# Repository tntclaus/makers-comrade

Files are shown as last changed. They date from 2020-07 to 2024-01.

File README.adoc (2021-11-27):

= Komrade of Maker (universal CNC platform)

[.right]
.First prototype, build volume (mm) 580x580x580
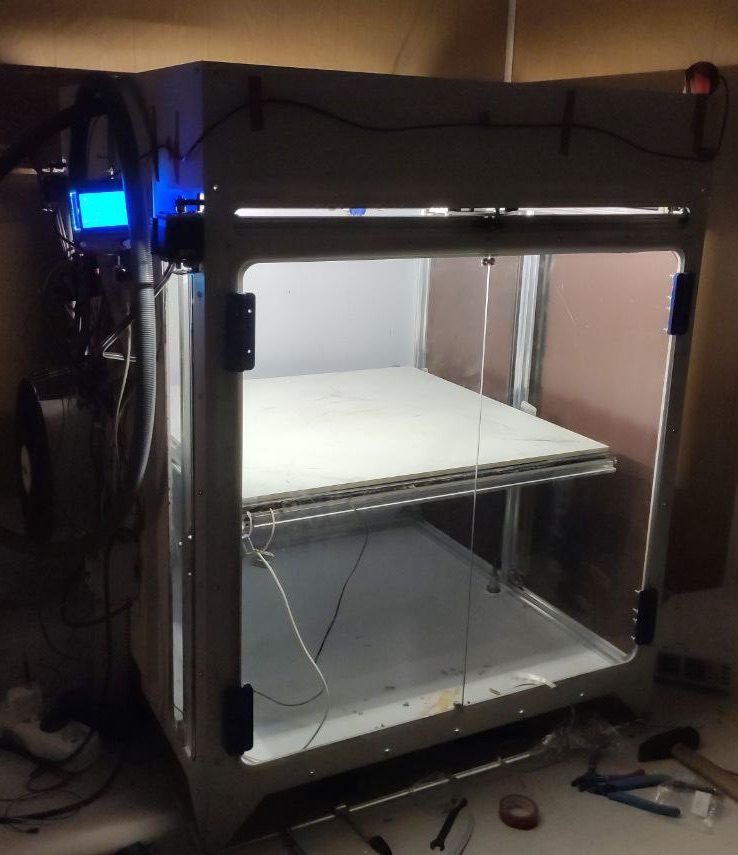
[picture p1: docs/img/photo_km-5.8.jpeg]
First prototype


This design is universal platform, that uses where available affordable parts, primarily from Reprap project, 8 bit realtime controllers, RPi 3/4 and Klipper.

Primary characteristics by application:

* 3D printing:
** Enclosed chamber passively heated up to 80ºC;
** Filament motion control;
** Auto bed levelling with Piezo Sensor and triple z axis;
** X/Y Linear speeds up to 200 mm/s (or greater with proper voltage/servos);
** Ceramic build surface.
* Milling with 585 series motors:
** Soft materials, e.g.: sheet plastics, plywood, aluminium (not tested);
** PCB prototyping.
* Laser cutting/engraving.
* Electrochemical machining.

== BOM
=== Base vitamins

.Base components common for all models
[cols="5,1,1,1",options="header",]
|===
|Part |Amount |Aliexpress |Amazon
|RAMPS 1.6+ |1 | - |-
|Arduino Mega |1 | - | -
|HDMI LCD 7" |1 | - | -
|RPi 3/4 |1 | - | -
|RPi Camera |1 | - | -
|RPi Motor Shield |1 | - | -
|Nema 17 steppers |5 | - | -
|X/Y axis MKS-Servo 42C |2 | - | -
|TMC 2209 |4 | - | -
|D16T parts set for universal X caret |1 | - | -
|V Slot Wheels|23 | - | -
|Steel parts for Z axis mount |1 | - | -
|Z axis axial bearing | 3 | - | -
|Z axis flexible coupler 5*8 |3 | - | -
|steel ball ø8mm |3 | - | -
|===

.Orbiter Extruder 3D Printer Toolhead
[cols="5,1,1,1",options="header",]
|===
|Part |Amount |Aliexpress |Amazon
|Extruder Orbiter with LDO stepper |1 | - | -
|Filament motion sensor |1 | - | -
|Crazy NF hotend | 1 | - | -
|===

=== Model KМ—3

Build Volume (mm): 300x300x300

[cols=",,,",options="header",]
|===
|Part |Amount |Aliexpress |Amazon
|  leadscrew  350 mm|  3  |  - | -
|  2020 VSlot extrusion 450 mm | 12 | - | -
|  2020 VSlot extrusion 850 mm | 4 | - | -
|  2040 VSlot extrusion 450 mm | 2 | - | -
|  GT6 Gates Belt (m) |  3  |  - | -
|===

=== Model KМ—6

Build Volume (mm): 600x600x600

== Dependencies

https://github.com/nophead/NopSCADlib
https://github.com/openscad/scad-utils
https://github.com/oysteinkrog/thing_libutils
https://github.com/Obijuan/obiscad

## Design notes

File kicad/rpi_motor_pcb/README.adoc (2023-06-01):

= Makers' Comrade CNC HAT

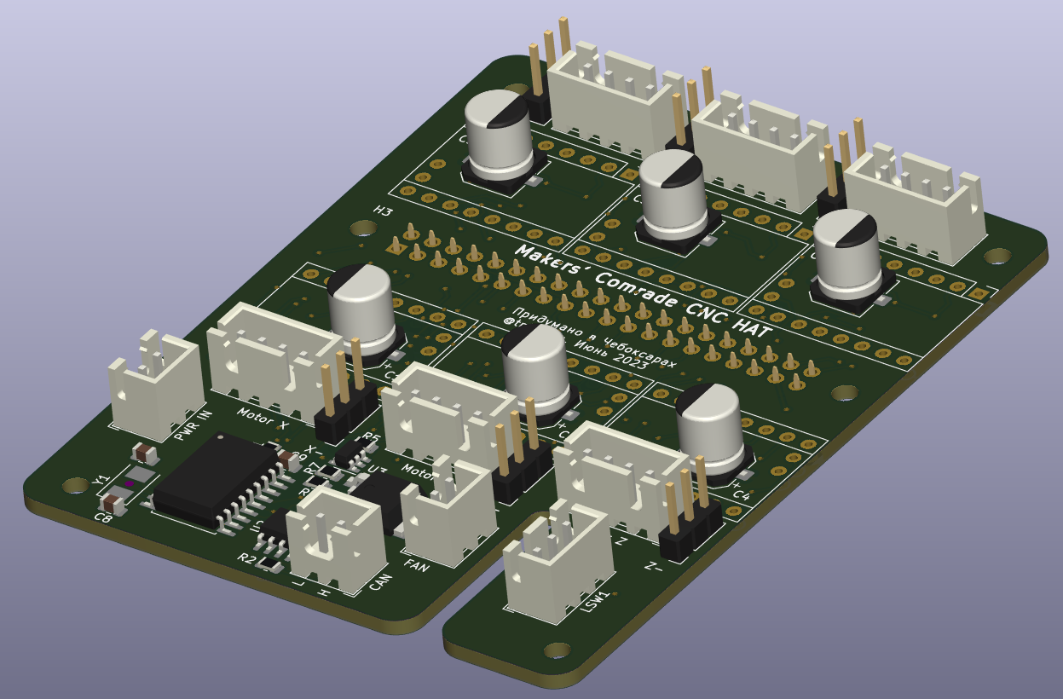
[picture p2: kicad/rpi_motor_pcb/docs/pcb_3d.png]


6-осевой ЧПУ шилд для Raspberry Pi 3B, 3B+, 4.

Возможности:

* Одновременное управление 6 драйверами шаговых двигателей:
** Поддерживаемые драйвера:
*** TMC2209, TMC2208 — режим UART с указанием адреса через перемычки MS1/MS2;
*** DRV8820, A4988 — обычный режим с конфигурацией через перемычки MS1,MS2,MS3;
* Любые другие драйвера, поддерживающие DIR/STEP.
* Суммарная пиковая производительность всех двигателей 1018 тыс. шагов/секунду (Klipper с патчем, Linux CNC не тестировался, но вероятно будет результат того же порядка).
* Поддержка концевиков для осей X, Y, Z, A, B, C как стандартного типа, так и DIAG выходов для без сенсорной парковки драйвера TMC2209.
* Поддержка дополнительного концевика (например, для датчика наличия/движения филамента 3д принтера).
* CANBUS host на базе MCP2515 и трансивера SN65HVD230:
** Даёт возможность гибкого дополнения станка периферией:
*** С контроллером экструдера https://github.com/makerbase-mks/MKS-THR36-THR42-UTC[MKS THR36] можно использовать как 3d принтер (не помешает canbus контроллер нагревательного стола/камеры).
*** С canbus контроллером шпинделя можно использовать как ЧПУ фрезер.
*** ...и т.д.
* Управление PWM нагрузкой с током до 1А (вентилятор обдува, маломощный двигатель).
* Поддерживаемые системы: Linux CNC, Klipper.

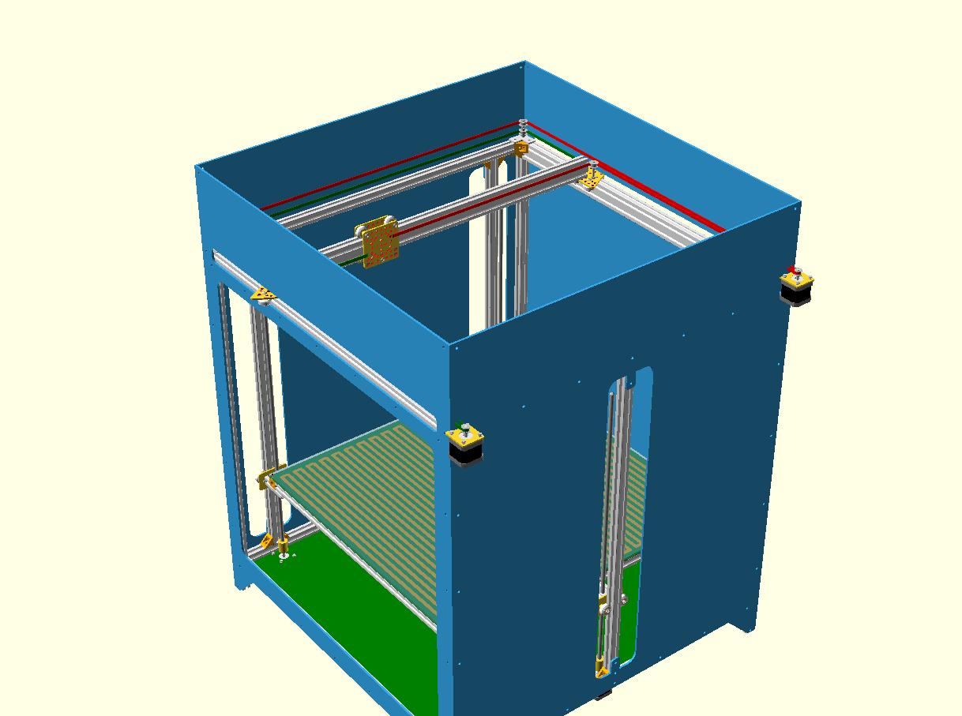
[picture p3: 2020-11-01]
scad/zap-3d-mk1.png

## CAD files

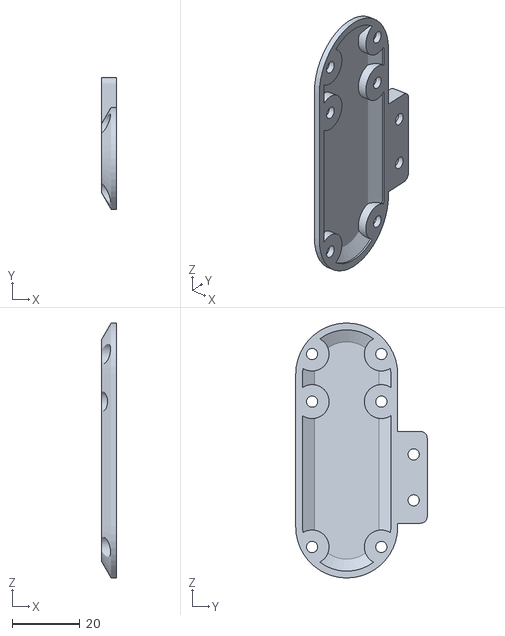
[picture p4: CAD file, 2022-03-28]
libstl/filament_sensor_cover_bmg.stl
4.55 x 38.7 x 75.0

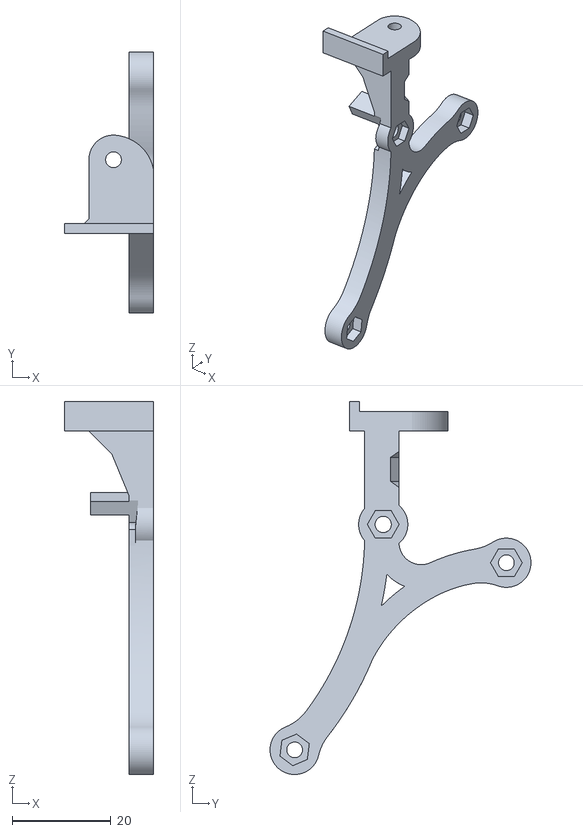
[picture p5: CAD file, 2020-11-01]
libstl/titan_vslot_bltouch_noctua_v2/Bras_fan.stl
18.2 x 53.0 x 75.7

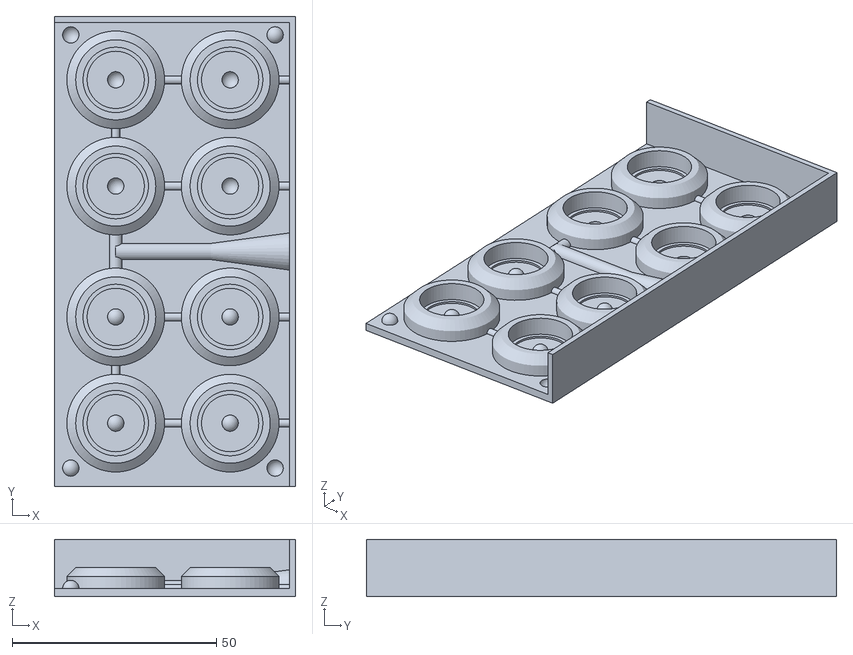
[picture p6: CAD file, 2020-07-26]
wheels_mold/v.4/wheels-mold.v4.stl
59.0 x 115.0 x 14.0

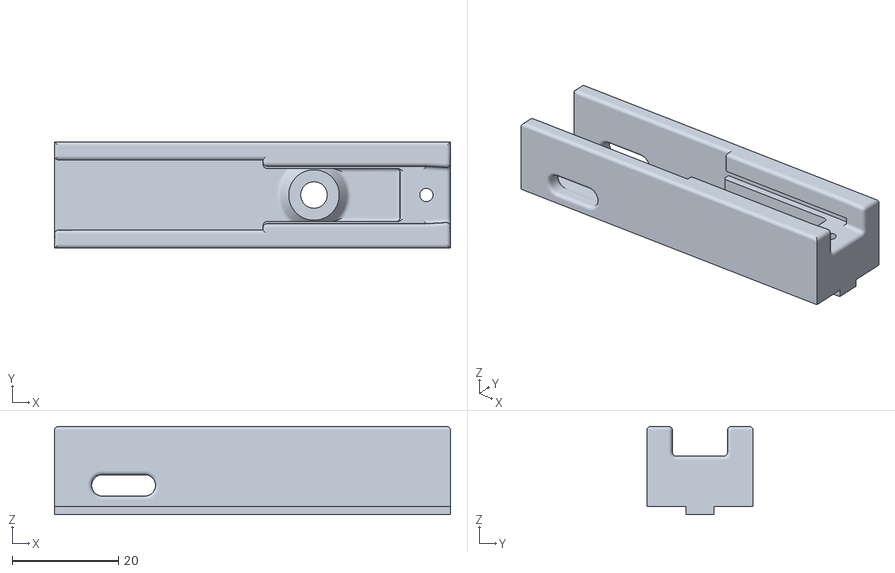
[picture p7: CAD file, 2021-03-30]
libstl/pp_uni_2.75_holder.stl
74.5 x 20.0 x 16.6

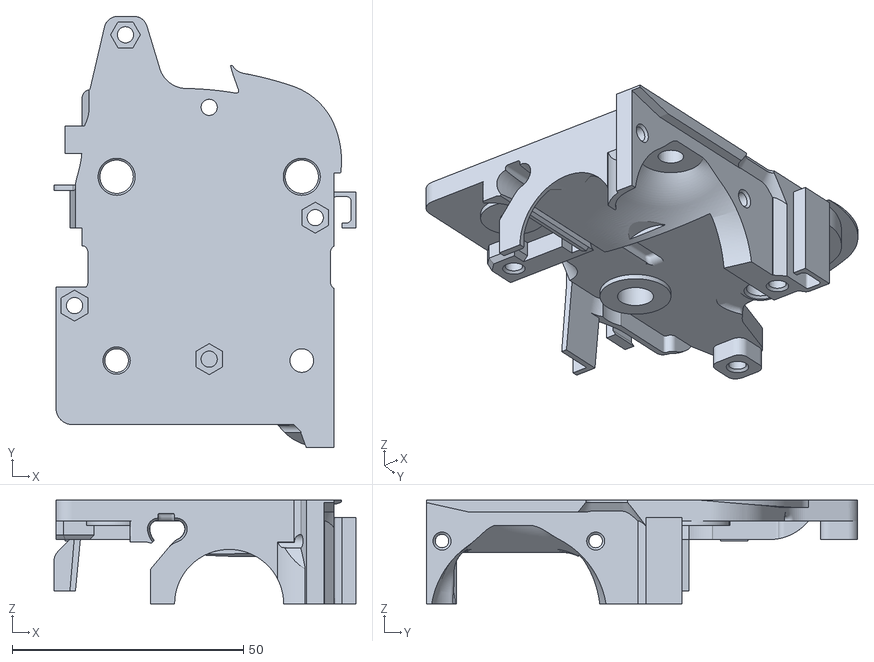
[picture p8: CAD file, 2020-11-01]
libstl/titan_vslot_bltouch_noctua_v2/Adapt_carriage.stl
65.2 x 93.2 x 22.4

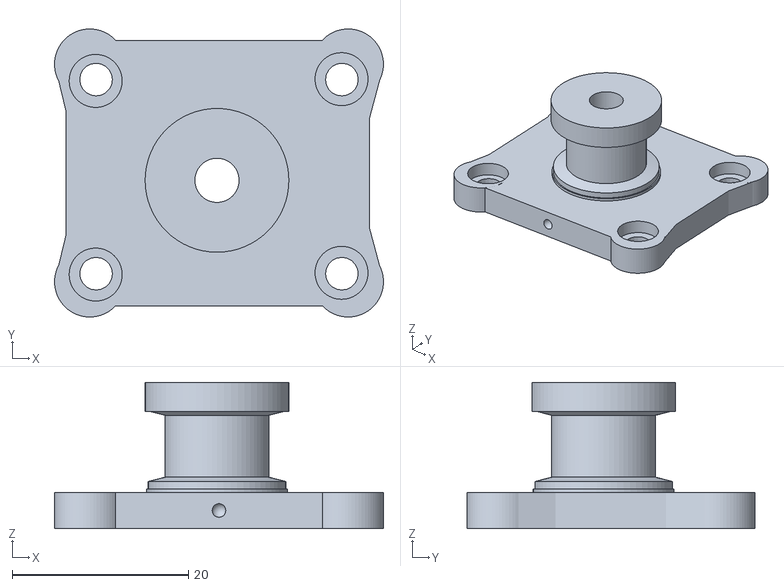
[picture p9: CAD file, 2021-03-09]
libstl/preicision_piezo_throat.stl
37.3 x 32.7 x 16.6

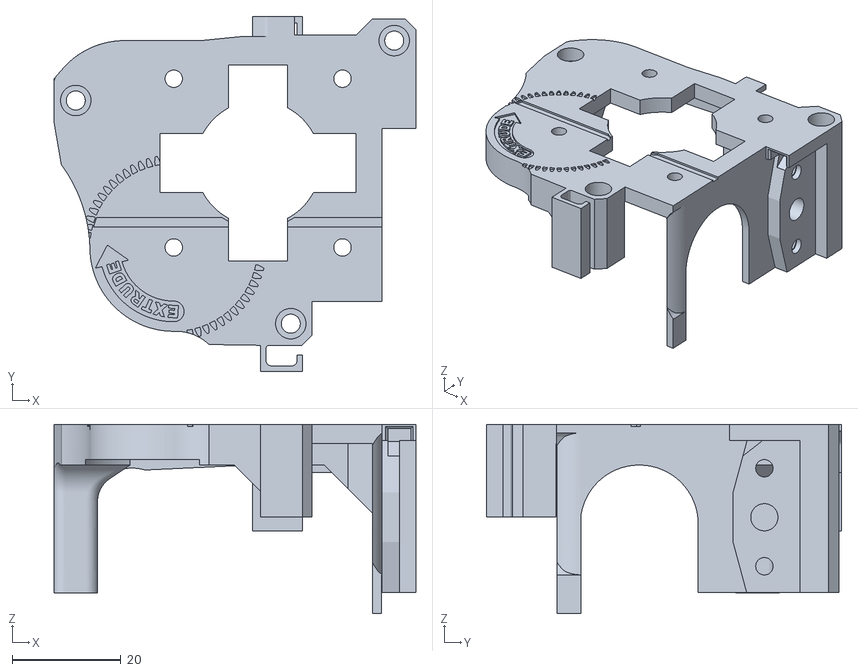
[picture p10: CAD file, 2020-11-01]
libstl/titan_vslot_bltouch_noctua_v2/Cover_titan.stl
66.5 x 65.2 x 34.8

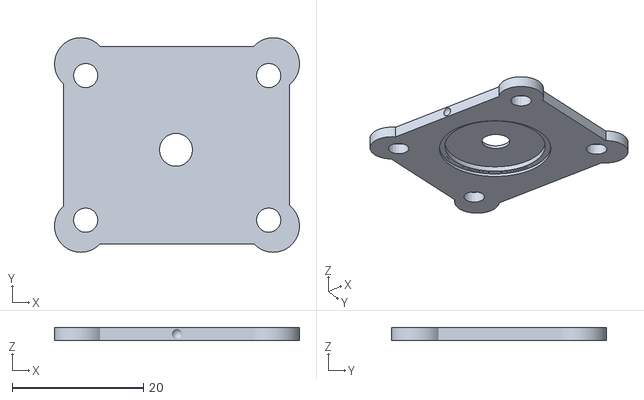
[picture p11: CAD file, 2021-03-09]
libstl/preicision_piezo_throat_bottom.stl
37.3 x 32.7 x 2.00

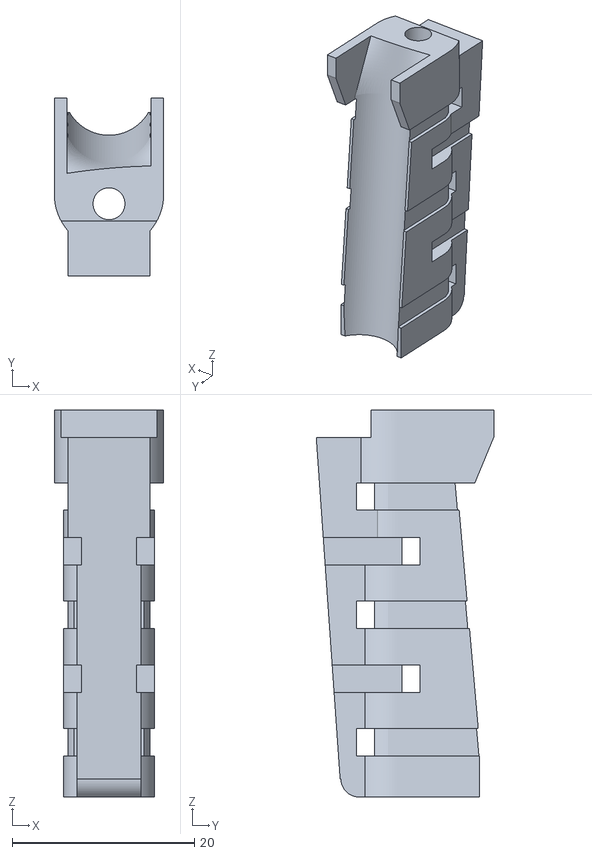
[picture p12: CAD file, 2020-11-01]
libstl/titan_vslot_bltouch_noctua_v2/Attache_cable.stl
12.0 x 19.5 x 42.5

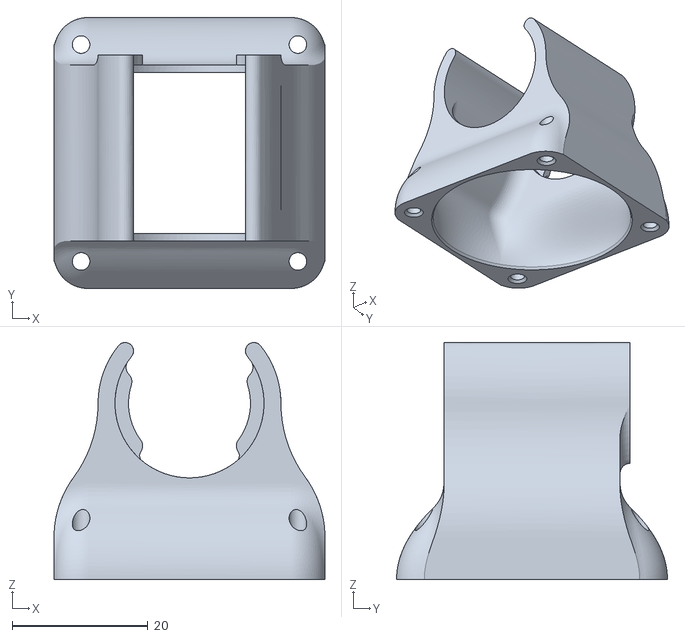
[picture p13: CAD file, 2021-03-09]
libstl/E3D_V6_40mm_Fan_v2.stl
40.0 x 40.0 x 35.0

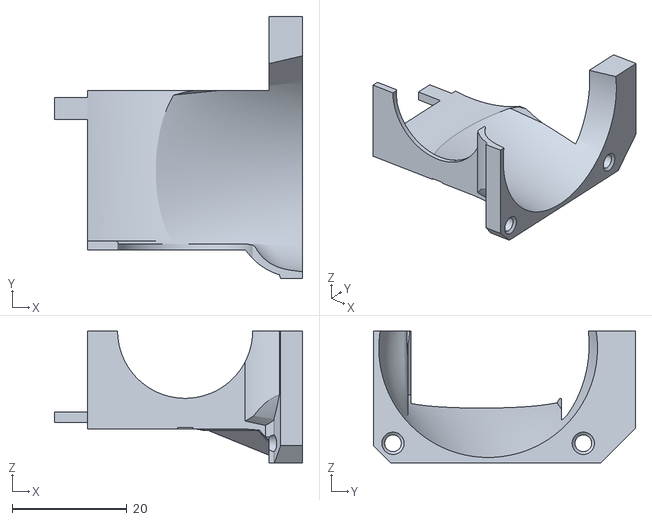
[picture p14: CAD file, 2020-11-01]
libstl/titan_vslot_bltouch_noctua_v2/Cover_e3d.stl
43.3 x 45.7 x 23.0

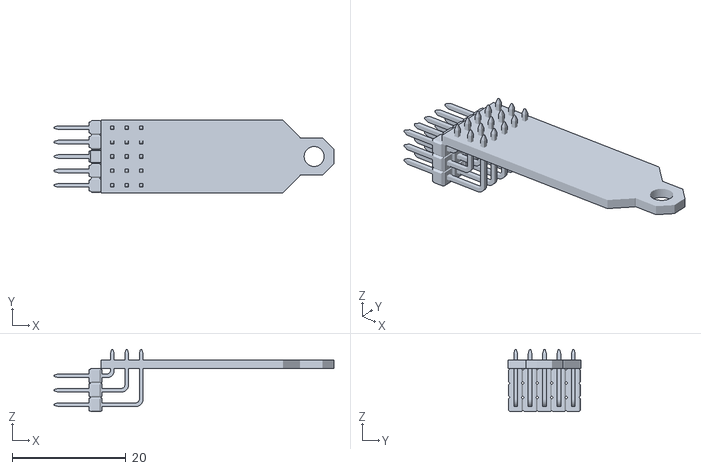
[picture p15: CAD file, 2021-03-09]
libstl/precision-piezo-uniboard2.75.stl
49.3 x 12.8 x 11.0

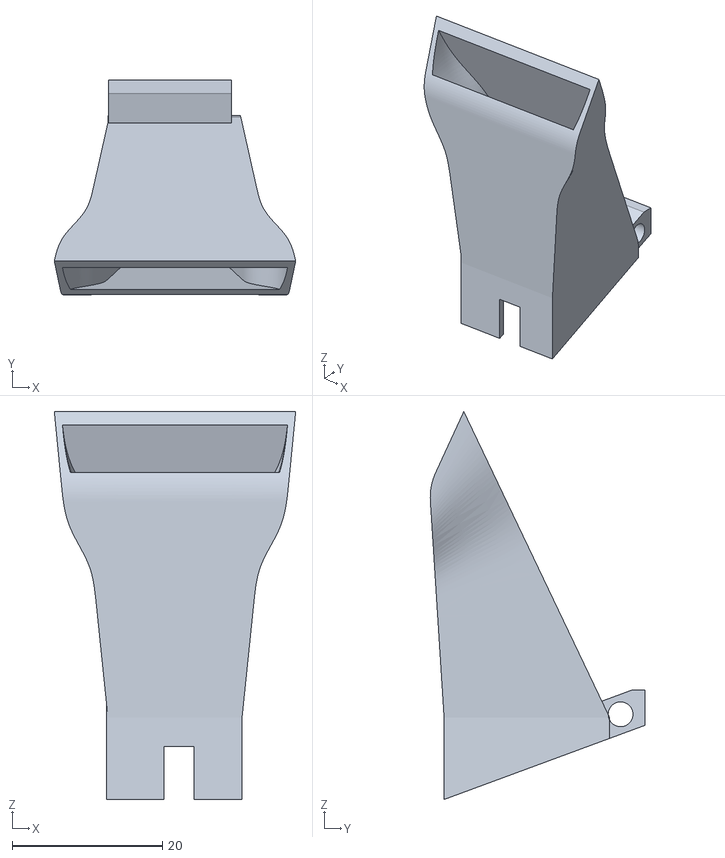
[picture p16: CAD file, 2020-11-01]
libstl/titan_vslot_bltouch_noctua_v2/Fan_duct.stl
32.1 x 28.5 x 51.6

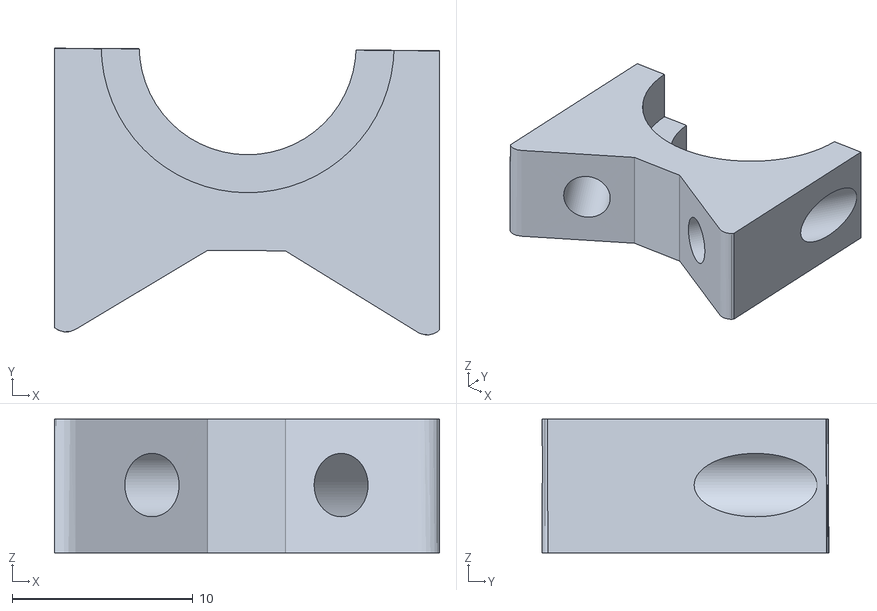
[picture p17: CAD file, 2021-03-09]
libstl/preicision_piezo_holder_inlet.stl
21.3 x 15.9 x 7.40

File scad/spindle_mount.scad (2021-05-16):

include <NopSCADlib/core.scad>
include <NopSCADlib/utils/rounded_polygon.scad>
include <NopSCADlib/vitamins/screws.scad>


include <../lib/utils.scad>
include <../lib/spindle/spindles.scad>

use <../lib/modularHoseLibrary.scad>
use <toolhead_utils.scad>

show_hose = false;


function TOOLHEAD_SPINDLE_RS895_VERTICAL_SCREW_MOUNTS(x = 30, y = 18) = [
    [ x,  y],
    [ x, -y],
    [-x,  y],
    [-x, -y],
];

coolant_hose_size = 20;
coolant_hose_size_out = coolant_hose_size+4;
coolant_hose_out_wall_dia = coolant_hose_size_out+2;

module motor_collet_44_100_30_RS895_stl() {
    $fn=180;
    
    motor_collet(
    width = 44, 
    length = 100, 
    heigth = 30, 
    type = RS895);
}

module motor_collet(width, length, heigth, wall_thickness = 30, type) {
    stl(
        str(
        "motor_collet","_",
        "W", width,"x",
        "L", length,"x",
        "H", heigth, "_",
        type[0])
    );
    
    
    collet_size = SPINDLE_motor_shield_diameter(type)+wall_thickness;
    
    color("#1111ff")
    render()
    difference() {
        cylinder(d = collet_size, h = heigth);
        translate_z(-1/2)
        cylinder(d = SPINDLE_motor_shield_diameter(type)+0.5, h = heigth+1);
        
        // половина
        translate([-collet_size/2+10, 0,collet_size])
        cube([collet_size, collet_size, collet_size*3], center = true);

        // срез сбоку
        translate([0, -collet_size/2-width/2,collet_size])
        cube([collet_size, collet_size, collet_size*3], center = true);

        // срез сбоку
        translate([0, collet_size/2+width/2,collet_size])
        cube([collet_size, collet_size, collet_size*3], center = true);

        // срез в центре
        translate([0, 0,collet_size])
        cube([collet_size, collet_size/3, collet_size*3], center = true);
        
        plate_corner_position(collet_size, width, 5);
        
        toolhead_screw_mount_locations(TOOLHEAD_SPINDLE_RS895_VERTICAL_SCREW_MOUNTS(),-heigth/2)
            cylinder(d = 4.01, h = heigth*2);

    }
}

module D16T_motor_mount_bottom_plate_W60xL100_IL80_ID8_CH8_VH11_RS895_dxf() {
    $fn = 180;
    motor_mount_bottom_plate_sketch(60, 100, 80, 8, 8, 11, RS895);
}

module D16T_motor_mount_top_plate_W60xL100_IL80_CH8_VH11_RS895_dxf() {
    $fn = 180;
    motor_mount_top_plate_sketch(60, 100, 80, 8, 11, RS895);
}

module motor_mount_bottom_plate_sketch(
    width, 
    length, 
    inset_length, 
    inset_depth, 
    coolant_hose_size,
    vacuum_hose_size,
    type) {
    coolant_hose_position = hose_position(length+1, coolant_hose_size, m=1);
    vacuum_hose_position = hose_position(length+5, vacuum_hose_size);


    difference() {
        toolhead_bottom_plate_sketch(width, length, inset_length, inset_depth);
        SPINDLE_cutouts(type);
        
        translate(coolant_hose_position)
        hose_base_plate_drill_holes(coolant_hose_size, 25, 3.05);
                    
        translate(vacuum_hose_position)    
        hose_base_plate_drill_holes(vacuum_hose_size, 25, 3.05); 
 
         toolhead_screw_mount_locations(TOOLHEAD_SPINDLE_RS895_VERTICAL_SCREW_MOUNTS())
            circle(d = 3.01);       
    }
}



module motor_mount_bottom_plate(
    width, 
    length, 
    inset_length, 
    inset_depth, 
    coolant_hose_size,
    vacuum_hose_size,
    type, 
    thickness = 3) {
    dxf(
        str(
        "D16T_motor_mount_bottom_plate","_",
        "W", width,"x",
        "L", length,"_",
        "IL", inset_length,"_",
        "ID", inset_depth,"_",
        "CH", coolant_hose_size, "_",
        "VH", vacuum_hose_size, "_",        
        type[0])
    );

    color("silver")
    translate_z(-3)
    linear_extrude(thickness)
    motor_mount_bottom_plate_sketch(
        width, 
        length, 
        inset_length, 
        inset_depth, 
        coolant_hose_size,
        vacuum_hose_size,
        type);
    coolant_hose_position = hose_position(length+1, coolant_hose_size, m=1);
    vacuum_hose_position = hose_position(length+5, vacuum_hose_size);


    
    plate_corner_position(width, length, 10)
    mount_magnet();
    
    
    if(show_hose) {
        translate_z(-thickness) {
            rotate([180,0,0]) translate(coolant_hose_position)
            coolant_hose_chain(coolant_hose_size);

            rotate([180,0,0]) translate(vacuum_hose_position)    
            rotate([0,0,180])
            vacuum_cleaner_hose_chain(vacuum_hose_size);
        }
    }
}

module motor_mount_top_plate_sketch(
        width, length, inset_length,
        coolant_hose_size,
        vacuum_hose_size, 
        type,
        thickness = 3
    ) {
    coolant_hose_position = hose_position(length+3, coolant_hose_size, m=1);
    vacuum_hose_position = hose_position(length+10, vacuum_hose_size);


    difference() {
        toolhead_top_plate_sketch(width, inset_length);
        circle(d = SPINDLE_motor_shield_diameter(type));
        

        translate(coolant_hose_position) hull() {
            circle(d = coolant_hose_size+4);
            translate([coolant_hose_size, 0, 0])
            circle(d = coolant_hose_size+4);
        }
                
        translate(vacuum_hose_position) hull() {   
            circle(d = vacuum_hose_size+4);
            translate([-vacuum_hose_size, 0, 0])
            circle(d = vacuum_hose_size+4);
        }
        
        toolhead_screw_mount_locations(TOOLHEAD_SPINDLE_RS895_VERTICAL_SCREW_MOUNTS())
            circle(d = 4.01);
    }    
}

module motor_mount_top_plate(
        width, length, inset_length,
        coolant_hose_size,
        vacuum_hose_size, 
        type,
        thickness = 3
    ) {
    dxf(
        str(
        "D16T_motor_mount_top_plate","_",
        "W", width,"x",
        "L", length,"_",
        "IL", inset_length,"_",
        "CH", coolant_hose_size, "_",
        "VH", vacuum_hose_size, "_",     
        type[0])
    );

    color("#aaaaaa")
    linear_extrude(thickness)
    motor_mount_top_plate_sketch(
        width, length, inset_length,
        coolant_hose_size,
        vacuum_hose_size, 
        type,
        thickness
    );
        
//    plate_corner_position(width, inset_length, 10)
//    translate_z(3)
//    mount_magnet();
//    translate([length/2-20, width/2-10, -2])
    toolhead_screw_mount_locations(TOOLHEAD_SPINDLE_RS895_VERTICAL_SCREW_MOUNTS())
    translate_z(-0.45)
    piezo_disc();
}

module coolant_hose_chain(size) {
    angle = 15;
    $fn = 20;
    color("blue") {
        translate_z(-3)
        rotate([180,0,0])
        hose_base_plate(size, 22, 3.05, 4.5);
        
        hose_base_plate(size, 22, 3.05, 4.5)
        rotate([0,angle,-angle])
        hose_segment(size)
        rotate([0,angle,-angle])
        hose_segment(size)
        rotate([0,-2*angle,-angle])
        hose_segment(size)
        rotate([0,-2*angle,angle])
        hose_segment(size)
        rotate([0,-2*angle,angle])
        hose_segment(size)
        rotate([0,-2*angle,2*angle])
        hose_round_nozzle(size, 3);
    }
}

module vacuum_cleaner_hose_chain(size) {
    angle = 15;
    $fn = 20;
    color("green") {
        translate_z(-3)
        rotate([180,0,0])
        hose_base_plate(size, 24, 3.05, 5.5);
        
        hose_base_plate(size, 24, 3.05, 5.5)
        rotate([0,angle,-angle])
        hose_segment(size)
        rotate([0,angle,-angle])
        hose_segment(size)
        rotate([0,-2*angle,-angle])
        hose_segment(size)
        rotate([0,-2*angle,angle])
        hose_segment(size)
        rotate([0,-2*angle,angle])
        hose_segment(size)
        rotate([0,-2*angle,2*angle])
        hose_flat_nozzle(size, size*2, size/2);
    }
}

module spindle_assembly(
        width, 
        length, 
        inset_length, 
        inset_depth, 
        heigth, 
        type = RS895
    ) {
    
    coolant_hose_size = 8;
    vacuum_hose_size = 12;

    toolhead_screw_mount_locations(TOOLHEAD_SPINDLE_RS895_VERTICAL_SCREW_MOUNTS(), 33)
        screw(M4_cap_screw, 35);

    
//    SPINDLE_ER11_assembly(type);
    motor_mount_bottom_plate(        
        width = width, length = length, inset_length = inset_length, type = type,
        coolant_hose_size = coolant_hose_size,
        vacuum_hose_size = vacuum_hose_size,
        inset_depth = inset_depth
    );    
    
    
    motor_collet(width-inset_depth*2, length, heigth, type = type);
    mirror([1,0,0])
    motor_collet(width-inset_depth*2, length, heigth, type = type);

    translate_z(heigth)
    motor_mount_top_plate(
        width = width, length = length, inset_length = inset_length, type = type,
        coolant_hose_size = coolant_hose_size,
        vacuum_hose_size = vacuum_hose_size
   );
}

//spindle_assembly(
//    width = 60, 
//    length = 100, 
//    inset_length = 80, 
//    inset_depth = 8, 
//    heigth = 30);

//D16T_motor_mount_bottom_plate_W60xL100_IL80_ID8_CH8_VH11_RS895_dxf();
//D16T_motor_mount_top_plate_W60xL100_IL80_CH8_VH11_RS895_dxf();
motor_collet_44_100_30_RS895_stl();

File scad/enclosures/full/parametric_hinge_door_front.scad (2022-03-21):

// -------------------------------------+---------------------------------------+---------------------------------------+---------------------------------------
// Title:        Parametric Caged Bearing
// Version:      3.7
// Release Date: 2019-12-14 (ISO 8601)
// Author:       Rohin Gosling
// -------------------------------------+---------------------------------------+---------------------------------------+---------------------------------------
//
// Description:
//
// - Parametric butt hinge, designed to be printed in one step.
//
// - While the entire working hinge may be printed in one step, it is also possible to disabled the internal fused pin, and leave a shaft
//   which may be used in the case where an external pin is desired.
//
// Release Notes:
//
// - Version 3.7
//   * Added a comment for the "knuckle_count" parameter, to notify users to always set an odd knuckle count in order to ensure that the unified
//     pin is supported by male knuckles on both ends. An even number of knuckles will leave one end of the unified pin unsupported by a male knuckle.
//   * Added a constraint to the "knuckle_count" parameter, to force an odd knuckle count. Even knuckle counts are now incemented to next odd number.
//     Example:
//     - A knuckle count of 4, will be incremented to 5.
//     - A knuckle count of 10 will, with be incremented to 11
//
// - Version 3.6
//   * Removed extended ASCII characters to make the source code compatible with the UTF-8 encoding required by the Thingiverse Customizer.
//
// - Version 3.5
//   * For hexagonal counterbores, the hexagonal cut has been rotated 90 degrees, to reduce the need for support material.
//     The overhang angle for hexagonal counterbore is 60 degrees.
//
// - Version 3.4
//   * Added support for linear and parabolic gusset curves.
//   * Factored out all SCG (Solid Constructive Geometry) overlap constants, and consolidated them into one global constant, "SCG_OVERLAP".
//
// - Version 3.3
//   * Placed pin shaft parameters into their own parameter group in the Thingiverse Customizer.
//
// - Version 3.2
//   * Added support for independently configurable top and bottom pin shaft counterbores.
//   * Added an assembly option to flip the model about the z-axis.
//     Usefull for viewing the top and bottom pin shaft counterbores.
//   * Configured the hinge throw angle Thingiverse Customizer parameter step size, to 5 degrees.
//
// - Version 3.1
//   * Added a counterbore feature for the pin shaft.
//     - While this feature may be enabled for one piece hinges that have the fused pin enabled, it is primarily designed for use with two
//       piece configurations that have their pin disabled. For instance, when the hinge is to be assembled using an external pin.
//     - In the case where a hinge is to be assembled using an external pin, it may be desired to have a pin shaft counterbore, where the end
//       caps of the knuckle joint array are counterbored, in order to allow the pin or bolt heads of the pin shaft, to be set flush with the
//       top and bottom edges of the hinge leaves.
//     - To accommodate both hexagonal and square bolt heads and nuts, the counterbore may be set to any one of circular, square or hexagonal.
//   * Added private text feature.
//     - A public parameter for the Thingiverse Customizer has not been added yet, however, users may set the 'text_enabled' local variable
//       in the 'leaf' module to 'true', which will enable a single row of inscribed text on each leaf.
//     - By default this feature will only work when exactly 4 fastener holes have been selected via the 'fastener_count' parameter, simply
//       because there is a nice open space available between the fastener holes for placing text, when 4 fastener holes are chosen.
//     - Text for the male and female leaves may be specified independently.
//
// - Version 3.0
//   * Added a parameter to disable the hinge pin, for when users would like to assemble with an external pin.
//   * Changed the main Thingiverse Customizer parameter group name from "Hinge Options", to "Assembly Options".
//   * Added a parameter to set the hinge throw angle.
//     Users can now set the throw angle, either for analysis and visualisation purposes, or for when the hinge is to be printed vertically
//     standing up on edge, in which case a throw angle of 120 degrees may be used to help keep the hinge stable on the build plate.
//   * Corrected spelling errors in the comments.
//
// - Version 2.9
//   * Added support for parabolic knuckle gussets to strengthen the knuckle joints.
//     Knuckle gussets may now be toggled on and off with the 'enable_knuckle_gusset' parameter.
//
// - Version 2.8
//   * Added the parameter, 'fastener_column_count', to enable single column fastener arrangements, that can be used for
//     piano hinge style fastener arrangements.
//
// - Version 2.7
//   * Rewrote the knuckle cutter module using mode generic math, that enables more parametizable control over knuckle joint
//     dimensions and configuration.
//
// - Version 2.6
//   * Added support for countersunk fastener holes. Now users can select either counterbore or countersunk.
//     dimensions and configuration.
//   * Started tracking release updates.
//
// - Version 1.0 - 2.5
//   * N/A - Release updates not tracked.
//
// -------------------------------------+---------------------------------------+---------------------------------------+---------------------------------------

// -------------------------------------+---------------------------------------+---------------------------------------+---------------------------------------
// Constants:
// -------------------------------------+---------------------------------------+---------------------------------------+---------------------------------------

// System constants.

C_CONSTANT = 0 + 0;     // Used to hide constant values from Thingiverse. Add to other constants to hide them as well.
C_NONE     = C_CONSTANT + 0;

// Leaf gender.

C_FEMALE   = C_CONSTANT + 0;
C_MALE     = C_CONSTANT + 1;

// SCG constants.

SCG_OVERLAP = C_CONSTANT + 0.01;    // Used for overlapping Boolean operations in order to avoid Boolean edge artefacts.
C_NEGATIVE  = C_CONSTANT + 0;       // Used for subtractive Boolean tools.
C_POSITIVE  = C_CONSTANT + 1;       // Used for additive Boolean tools.

// Bolt head shapes.

C_CIRCULAR  = C_CONSTANT + 0;
C_SQUARE    = C_CONSTANT + 1;
C_HEXAGONAL = C_CONSTANT + 2;

// Curve Type

C_FUNCTION_LINEAR    = C_CONSTANT + 1;      //  y = ax + b
C_FUNCTION_CIRCULAR  = C_CONSTANT + 2;      // r2 = x2 + y2
C_FUNCTION_PARABOLIC = C_CONSTANT + 3;      //  y = a2(x - j)2 + k    ...Vertex form.

// Minimum and maximum constraints.

C_MIN_HINGE_WIDTH                          = C_CONSTANT + 1.0;
C_MIN_HINGE_HEIGHT                         = C_CONSTANT + 1.0;
C_MIN_LEAF_GAUGE                           = C_CONSTANT + 1.0;
C_MIN_COMPONENT_CLEARENCE                  = C_CONSTANT + 0.1;
C_MAX_COMPONENT_CLEARENCE                  = C_CONSTANT + 1.0;
C_MIN_KNUCKLE_COUNT                        = C_CONSTANT + 3;
C_MAX_KNUCKLE_COUNT                        = C_CONSTANT + 15;
C_MIN_KNUCKLE_GUSSET_WIDTH                 = C_CONSTANT + 1.0;
C_MIN_FASTENER_MARGIN                      = C_CONSTANT + 1.0;
C_MIN_PIN_DIAMETER                         = C_CONSTANT + 1.0;
C_MIN_COUNTER_SINK_DEPTH_STOP              = C_CONSTANT + 1.0;
C_MIN_FASTENER_THREAD_DIAMETER             = C_CONSTANT + 0.0;
C_MIN_FASTENER_COUNT                       = C_CONSTANT + 3;
C_MIN_FASTENER_COLUMN_COUNT                = C_CONSTANT + 1;
C_MAX_FASTENER_COLUMN_COUNT                = C_CONSTANT + 2;
C_MIN_TESSELLATION                         = C_CONSTANT + 32;
C_MAX_TESSELLATION                         = C_CONSTANT + 256;
C_MIN_THROW_ANGLE                          = C_CONSTANT + -90;
C_MAX_THROW_ANGLE                          = C_CONSTANT + 180;
C_DEFAULT_THROW_ANGLE                      = C_CONSTANT + 0;
C_MIN_PIN_SHAFT_COUNTERBORE_DIAMETER       = C_CONSTANT + 0.1;
C_MIN_PIN_SHAFT_COUNTERBORE_WALL_THICKNESS = C_CONSTANT + 0.3;
C_MIN_PIN_SHAFT_COUNTERBORE_DEPTH          = C_CONSTANT + 0.0;
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

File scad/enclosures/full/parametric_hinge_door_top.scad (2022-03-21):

// -------------------------------------+---------------------------------------+---------------------------------------+---------------------------------------
// Title:        Parametric Caged Bearing
// Version:      3.7
// Release Date: 2019-12-14 (ISO 8601)
// Author:       Rohin Gosling
// -------------------------------------+---------------------------------------+---------------------------------------+---------------------------------------
//
// Description:
//
// - Parametric butt hinge, designed to be printed in one step.
//
// - While the entire working hinge may be printed in one step, it is also possible to disabled the internal fused pin, and leave a shaft
//   which may be used in the case where an external pin is desired.
//
// Release Notes:
//
// - Version 3.7
//   * Added a comment for the "knuckle_count" parameter, to notify users to always set an odd knuckle count in order to ensure that the unified
//     pin is supported by male knuckles on both ends. An even number of knuckles will leave one end of the unified pin unsupported by a male knuckle.
//   * Added a constraint to the "knuckle_count" parameter, to force an odd knuckle count. Even knuckle counts are now incemented to next odd number.
//     Example:
//     - A knuckle count of 4, will be incremented to 5.
//     - A knuckle count of 10 will, with be incremented to 11
//
// - Version 3.6
//   * Removed extended ASCII characters to make the source code compatible with the UTF-8 encoding required by the Thingiverse Customizer.
//
// - Version 3.5
//   * For hexagonal counterbores, the hexagonal cut has been rotated 90 degrees, to reduce the need for support material.
//     The overhang angle for hexagonal counterbore is 60 degrees.
//
// - Version 3.4
//   * Added support for linear and parabolic gusset curves.
//   * Factored out all SCG (Solid Constructive Geometry) overlap constants, and consolidated them into one global constant, "SCG_OVERLAP".
//
// - Version 3.3
//   * Placed pin shaft parameters into their own parameter group in the Thingiverse Customizer.
//
// - Version 3.2
//   * Added support for independently configurable top and bottom pin shaft counterbores.
//   * Added an assembly option to flip the model about the z-axis.
//     Usefull for viewing the top and bottom pin shaft counterbores.
//   * Configured the hinge throw angle Thingiverse Customizer parameter step size, to 5 degrees.
//
// - Version 3.1
//   * Added a counterbore feature for the pin shaft.
//     - While this feature may be enabled for one piece hinges that have the fused pin enabled, it is primarily designed for use with two
//       piece configurations that have their pin disabled. For instance, when the hinge is to be assembled using an external pin.
//     - In the case where a hinge is to be assembled using an external pin, it may be desired to have a pin shaft counterbore, where the end
//       caps of the knuckle joint array are counterbored, in order to allow the pin or bolt heads of the pin shaft, to be set flush with the
//       top and bottom edges of the hinge leaves.
//     - To accommodate both hexagonal and square bolt heads and nuts, the counterbore may be set to any one of circular, square or hexagonal.
//   * Added private text feature.
//     - A public parameter for the Thingiverse Customizer has not been added yet, however, users may set the 'text_enabled' local variable
//       in the 'leaf' module to 'true', which will enable a single row of inscribed text on each leaf.
//     - By default this feature will only work when exactly 4 fastener holes have been selected via the 'fastener_count' parameter, simply
//       because there is a nice open space available between the fastener holes for placing text, when 4 fastener holes are chosen.
//     - Text for the male and female leaves may be specified independently.
//
// - Version 3.0
//   * Added a parameter to disable the hinge pin, for when users would like to assemble with an external pin.
//   * Changed the main Thingiverse Customizer parameter group name from "Hinge Options", to "Assembly Options".
//   * Added a parameter to set the hinge throw angle.
//     Users can now set the throw angle, either for analysis and visualisation purposes, or for when the hinge is to be printed vertically
//     standing up on edge, in which case a throw angle of 120 degrees may be used to help keep the hinge stable on the build plate.
//   * Corrected spelling errors in the comments.
//
// - Version 2.9
//   * Added support for parabolic knuckle gussets to strengthen the knuckle joints.
//     Knuckle gussets may now be toggled on and off with the 'enable_knuckle_gusset' parameter.
//
// - Version 2.8
//   * Added the parameter, 'fastener_column_count', to enable single column fastener arrangements, that can be used for
//     piano hinge style fastener arrangements.
//
// - Version 2.7
//   * Rewrote the knuckle cutter module using mode generic math, that enables more parametizable control over knuckle joint
//     dimensions and configuration.
//
// - Version 2.6
//   * Added support for countersunk fastener holes. Now users can select either counterbore or countersunk.
//     dimensions and configuration.
//   * Started tracking release updates.
//
// - Version 1.0 - 2.5
//   * N/A - Release updates not tracked.
//
// -------------------------------------+---------------------------------------+---------------------------------------+---------------------------------------

// -------------------------------------+---------------------------------------+---------------------------------------+---------------------------------------
// Constants:
// -------------------------------------+---------------------------------------+---------------------------------------+---------------------------------------

// System constants.
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

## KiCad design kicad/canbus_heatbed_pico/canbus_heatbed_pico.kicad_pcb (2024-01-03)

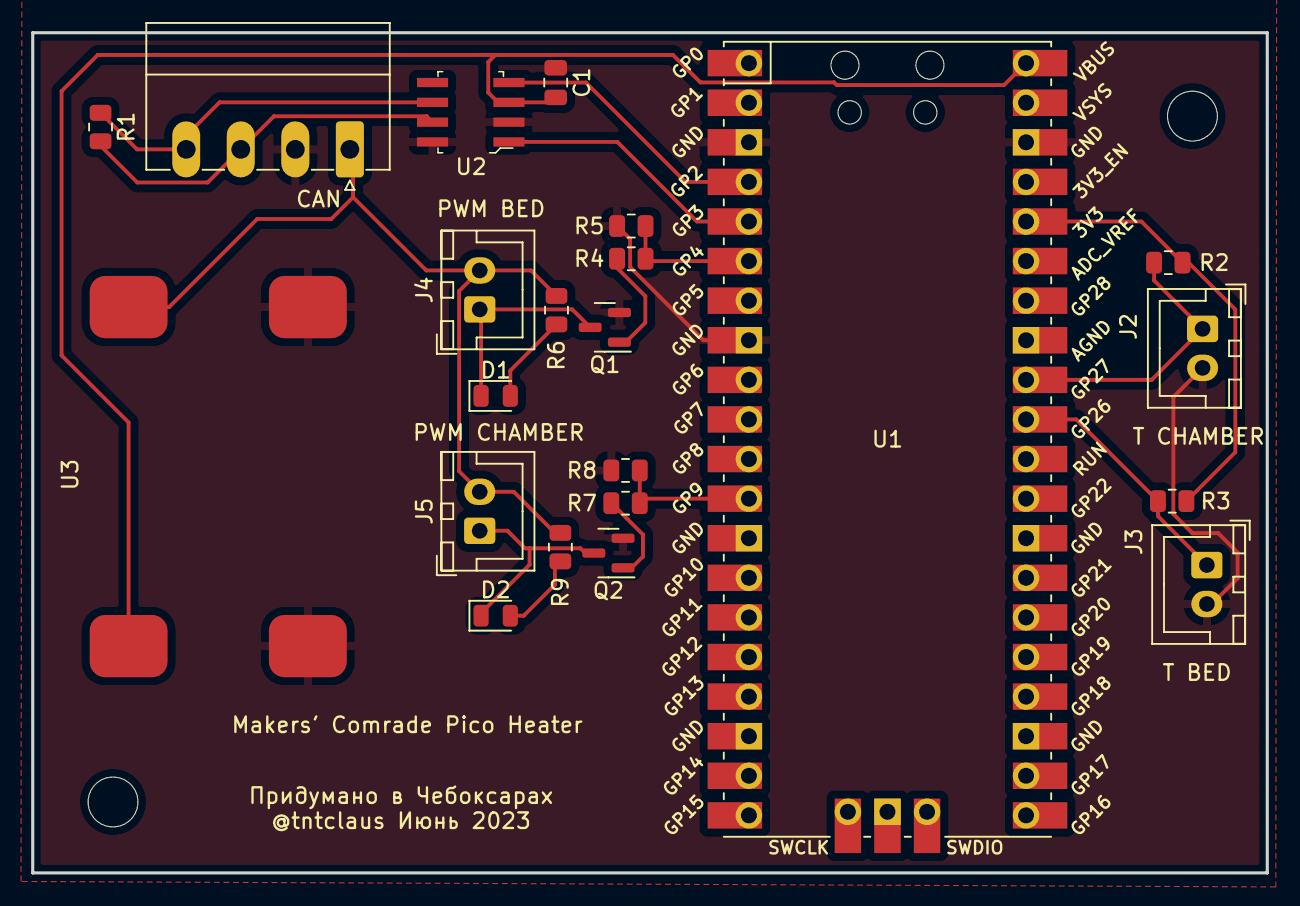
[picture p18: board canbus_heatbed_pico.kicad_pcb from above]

Board: 2 copper layers, 79.2 x 53.9 mm, 24 parts (0 on the bottom side), 18 nets.

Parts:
C1: 0.1µF; C_0805_2012Metric
D1, D2: XL-2012UGC; LED_0805_2012Metric
H1, H2: MountingHole; MountingHole_3.2mm_M3_DIN965
J1: CAN; PhoenixContact_MC_1,5_4-G-3.5_1x04_P3.50mm_Horizontal
J2: T CHAMBER; JST_XH_B2B-XH-A_1x02_P2.50mm_Vertical
J3: T BED; JST_XH_B2B-XH-A_1x02_P2.50mm_Vertical
J4: PWM BED; JST_XH_B2B-XH-A_1x02_P2.50mm_Vertical
J5: PWM CHAMBER; JST_XH_B2B-XH-A_1x02_P2.50mm_Vertical
Q1, Q2: 2N7002K; SOT-23
R1: 120; R_0805_2012Metric
R2, R3, R5, R6, R8, R9: 4.7k; R_0805_2012Metric
R4, R7: 200; R_0805_2012Metric
U1: Pico; RPi_Pico_SMD_TH
U2: SN65HVD230DR; SOIC-8_W3.9mm
U3: MP1584EN 5V; MP1584EN

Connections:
+3V3: R2.1, R3.1, U1.36 (3V3)
+5V: C1.2, U1.40 (VBUS), U2.3 (VCC), U3.1 (5V)
+24V: J1.1, J4.2, J5.2, R6.2, R9.2, U3.3 (Vin+)
/CAN_RX: U1.4 (GPIO2), U2.4 (R)
/CAN_TX: U1.5 (GPIO3), U2.1 (D)
/H: J1.4, R1.1, U2.6 (CANL)
/L: J1.3, R1.2, U2.7 (CANH)
/PWM BED: R4.1, R5.1, U1.6 (GPIO4)
/PWM CHAMBER: R7.1, R8.1, U1.12 (GPIO9)
/T BED: J3.1, R3.2, U1.31 (GPIO26_ADC0)
/T CHAMBER: J2.1, R2.2, U1.32 (GPIO27_ADC1)
GND: C1.1, J1.2, J2.2, J3.2, Q1.2 (S), Q2.2 (S), R5.2, R8.2, U1.3 (GND), U1.8 (GND), U1.38 (GND), U2.2 (GND), U2.8 (RS), U3.2 (GND), U3.4 (Vin-)
unnamed: D1.1 (K), J4.1, Q1.3 (D)
unnamed: D1.2 (A), R6.1
unnamed: D2.1 (K), J5.1, Q2.3 (D)
unnamed: D2.2 (A), R9.1
unnamed: Q1.1 (G), R4.2
unnamed: Q2.1 (G), R7.2

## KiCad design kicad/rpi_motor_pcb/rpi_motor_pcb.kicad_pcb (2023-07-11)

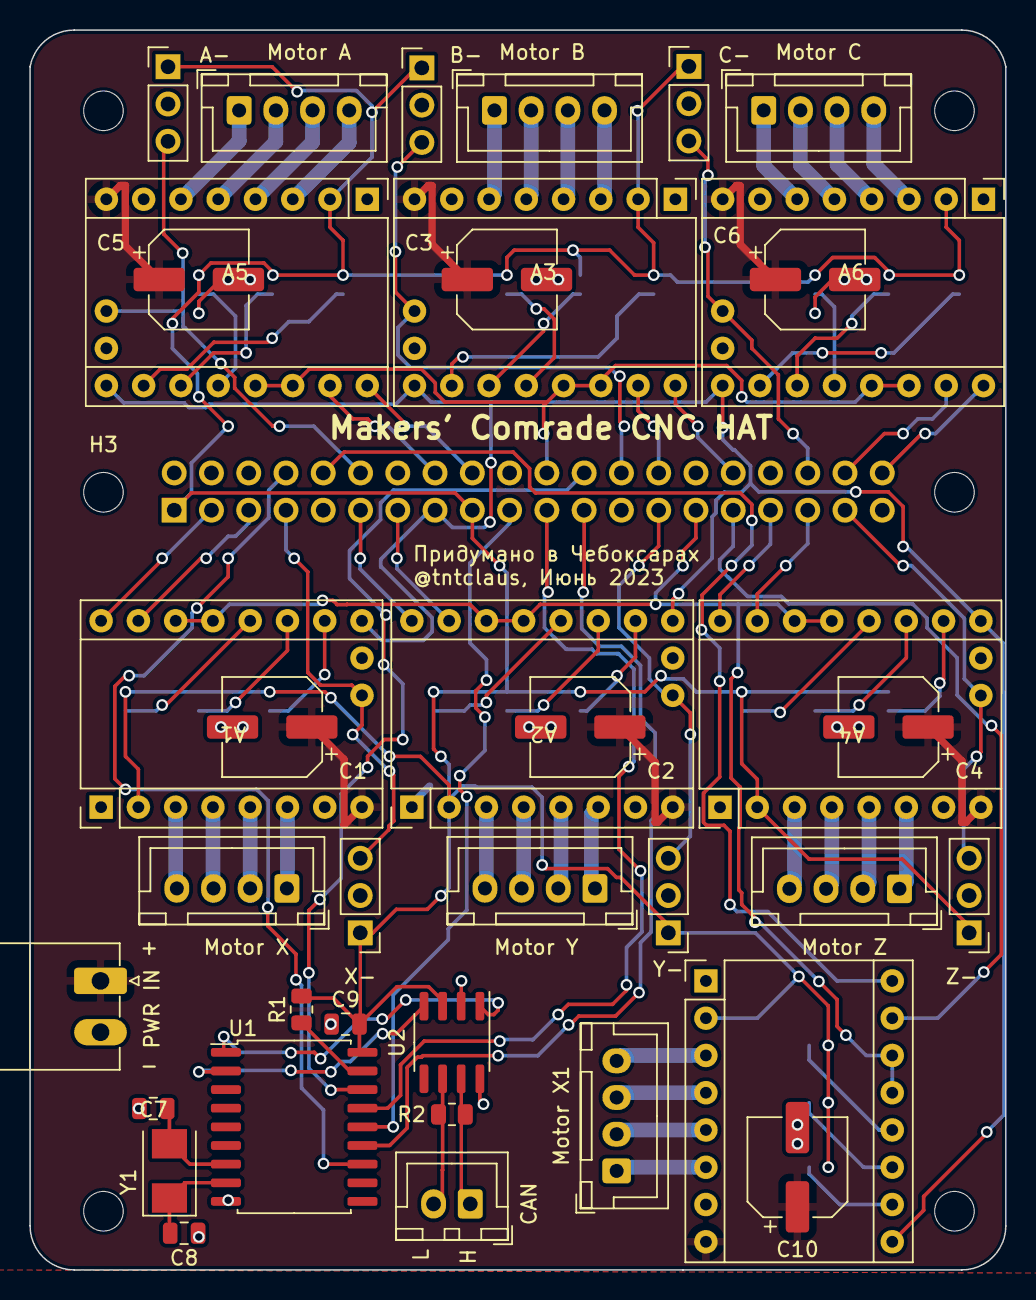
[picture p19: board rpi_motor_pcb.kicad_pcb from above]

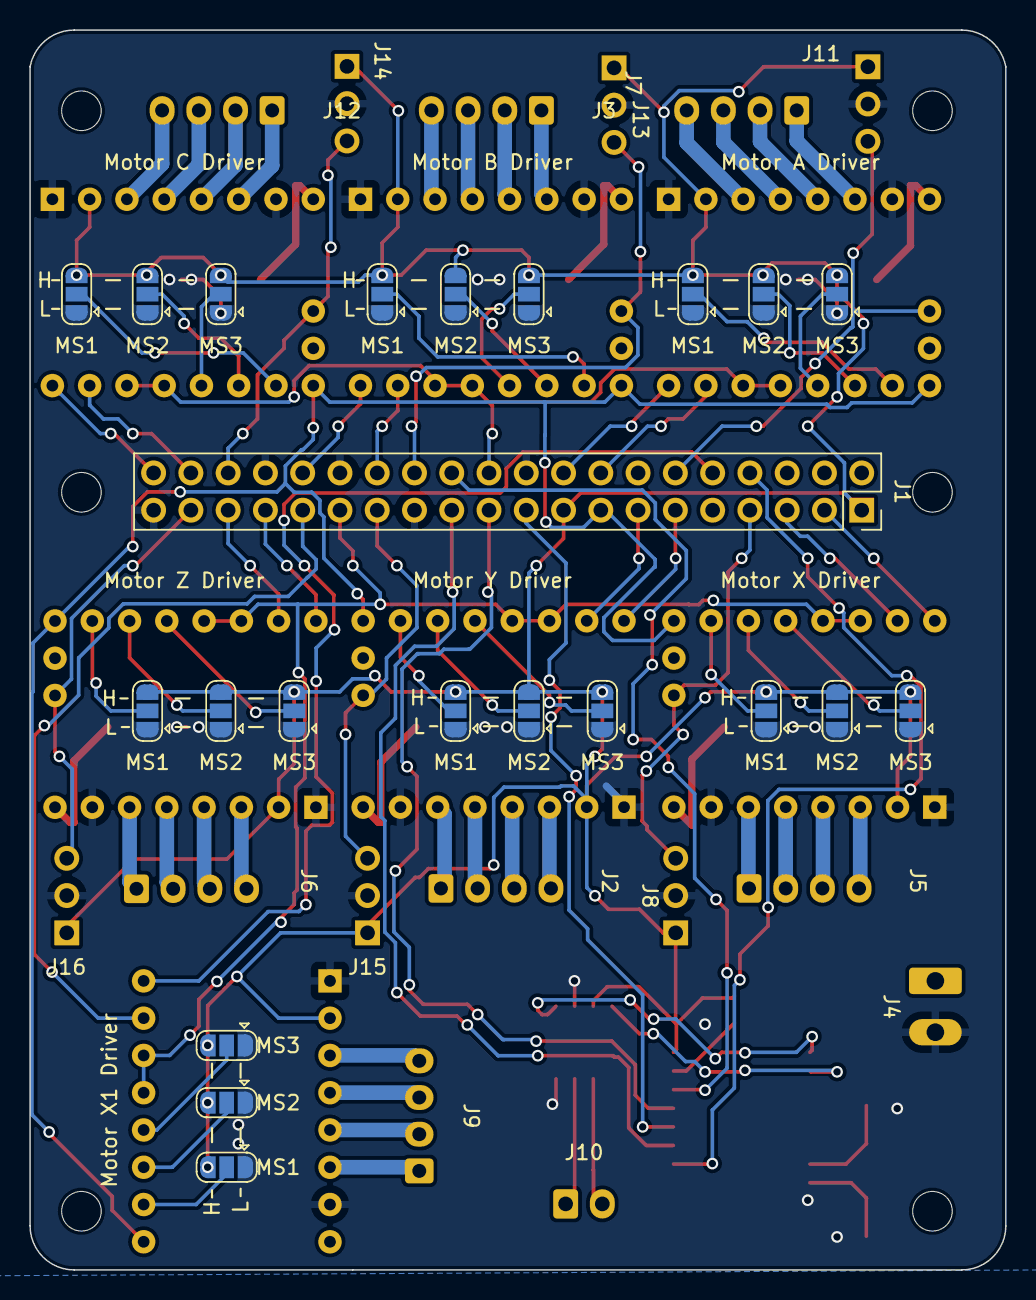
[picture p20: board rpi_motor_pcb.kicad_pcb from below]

Board: 2 copper layers, 66.5 x 84.5 mm, 65 parts (22 on the bottom side), 87 nets.

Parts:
A1: Motor X Driver; TMC220X
A2: Motor Y Driver; TMC220X
A3: Motor B Driver; TMC220X
A4: Motor Z Driver; TMC220X
A5: Motor A Driver; TMC220X
A6: Motor C Driver; TMC220X
A7: Motor X1 Driver; TMC2208
C1, C2, C3, C4, C5, C6, C10: 100µF 50V; CP_Elec_6.3x7.7
C7, C8: 22pF; C_0805_2012Metric
C9: 0.1µF; C_0805_2012Metric
H1, H2, H3, H4, H5, H6: MountingHole; MountingHole_2.7mm_M2.5_ISO14580
J1: Raspberry_Pi_2_3; PinSocket_2x20_P2.54mm_Vertical
J2: Motor Y; JST_XH_B4B-XH-A_1x04_P2.50mm_Vertical
J3: Motor B; JST_XH_B4B-XH-A_1x04_P2.50mm_Vertical
J4: PWR IN; PhoenixContact_MC_1,5_2-G-3.5_1x02_P3.50mm_Horizontal
J5: Motor X; JST_XH_B4B-XH-A_1x04_P2.50mm_Vertical
J6: Motor Z; JST_XH_B4B-XH-A_1x04_P2.50mm_Vertical
J7: Motor A; JST_XH_B4B-XH-A_1x04_P2.50mm_Vertical
J8: X-; PinHeader_1x03_P2.54mm_Vertical
J9: Motor X1; JST_XH_B4B-XH-A_1x04_P2.50mm_Vertical
J10: CAN; JST_XH_B2B-XH-A_1x02_P2.50mm_Vertical
J11: A-; PinHeader_1x03_P2.54mm_Vertical
J12: Motor C; JST_XH_B4B-XH-A_1x04_P2.50mm_Vertical
J13: B-; PinHeader_1x03_P2.54mm_Vertical
J14: C-; PinHeader_1x03_P2.54mm_Vertical
J15: Y-; PinHeader_1x03_P2.54mm_Vertical
J16: Z-; PinHeader_1x03_P2.54mm_Vertical
JP1, JP4, JP7, JP10, JP13, JP16, JP19: MS3; SolderJumper-3_P1.3mm_Open_RoundedPad1.0x1.5mm
JP2, JP5, JP8, JP11, JP14, JP17, JP20: MS2; SolderJumper-3_P1.3mm_Open_RoundedPad1.0x1.5mm
JP3, JP6, JP9, JP12, JP15, JP18, JP21: MS1; SolderJumper-3_P1.3mm_Open_RoundedPad1.0x1.5mm
R1: 10k; R_0805_2012Metric
R2: 120; R_0805_2012Metric
U1: MCP2515-xSO; SOIC-18W_7.5x11.6mm_P1.27mm
U2: SN65HVD230; SOIC-8_3.9x4.9mm_P1.27mm
Y1: Crystal; Crystal_SMD_5032-2Pin_5.0x3.2mm

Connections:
+3V3: A1.2 (VDD), A2.2 (VDD), A3.2 (VDD), A4.2 (VDD), A5.2 (VDD), A6.2 (VDD), A7.2 (VDD), C9.2, J1.1 (3V3), J1.17 (3V3), J8.1, J11.1, J13.1, J14.1, J15.1, J16.1, JP1.3 (B), JP2.3 (B), JP3.3 (B), JP4.3 (B), JP5.3 (B), JP6.3 (B), JP7.3 (B), JP8.3 (B), JP9.3 (B), JP10.3 (B), JP11.3 (B), JP12.3 (B), JP13.3 (B), JP14.3 (B), JP15.3 (B), JP16.3 (B), JP17.3 (B), JP18.3 (B), JP19.3 (B), JP20.3 (B), JP21.3 (B), R1.2, U1.18 (VDD), U2.3 (VCC)
/CAN/H: J10.1, R2.1, U2.7 (CANH)
/CAN/L: J10.2, R2.2, U2.6 (CANL)
/CAN/RX: U1.2 (RXCAN), U2.4 (R)
/CAN/TX: U1.1 (TXCAN), U2.1 (D)
/CAN_CS: J1.24 (~CE0/GPIO8), U1.16 (~CS)
/CAN_INT: J1.8 (GPIO14/TXD), U1.12 (~INT)
/CAN_MISO: J1.21 (MISO0/GPIO9), U1.15 (SO)
/CAN_MOSI: J1.19 (MOSI0/GPIO10), U1.14 (SI)
/CAN_SCK: J1.23 (SCLK0/GPIO11), U1.13 (SCK)
/MA DIAG: A5.18 (DIAG), J1.12 (GPIO18/PWM0), J11.3
/MA DIR: A5.16 (DIR), J1.18 (GPIO24)
/MA STEP: A5.15 (STEP), J1.16 (GPIO23)
/MB DIAG: A3.18 (DIAG), J1.26 (~CE1/GPIO7), J13.3
/MB DIR: A3.16 (DIR), J1.32 (PWM0/GPIO12)
/MB STEP: A3.15 (STEP), J1.28 (ID_SC/GPIO1)
/MC DIAG: A6.18 (DIAG), J1.36 (GPIO16), J14.3
/MC DIR: A6.16 (DIR), J1.40 (GPIO21/SCLK1)
/MC STEP: A6.15 (STEP), J1.38 (GPIO20/MOSI1)
/MX1 DIR: A7.16 (DIR), J1.10 (GPIO15/RXD)
/MX1 STEP: A7.15 (STEP), J1.31 (GCLK2/GPIO6)
/MX DIAG: A1.18 (DIAG), J1.7 (GCLK0/GPIO4), J8.3
/MX DIR: A1.16 (DIR), J1.3 (SDA/GPIO2)
/MX STEP: A1.15 (STEP), J1.5 (SCL/GPIO3)
/MY DIAG: A2.18 (DIAG), J1.27 (ID_SD/GPIO0), J15.3
/MY DIR: A2.16 (DIR), J1.11 (GPIO17)
/MY STEP: A2.15 (STEP), J1.13 (GPIO27)
/MZ DIAG: A4.18 (DIAG), J1.37 (GPIO26), J16.3
/MZ DIR: A4.16 (DIR), J1.33 (PWM1/GPIO13)
/MZ STEP: A4.15 (STEP), J1.35 (GPIO19/MISO1)
/Motor A/1A: A5.4 (1A), J7.3
/Motor A/1B: A5.3 (1B), J7.4
/Motor A/2A: A5.5 (2A), J7.2
/Motor A/2B: A5.6 (2B), J7.1
/Motor A/MS1: A5.10 (MS1), JP15.2 (C)
/Motor A/MS2: A5.11 (MS2), JP14.2 (C)
/Motor A/MS3: A5.12 (NC/TX), JP13.2 (C)
/Motor B/1A: A3.4 (1A), J3.3
/Motor B/1B: A3.3 (1B), J3.4
/Motor B/2A: A3.5 (2A), J3.2
/Motor B/2B: A3.6 (2B), J3.1
/Motor B/MS1: A3.10 (MS1), JP9.2 (C)
/Motor B/MS2: A3.11 (MS2), JP8.2 (C)
/Motor B/MS3: A3.12 (NC/TX), JP7.2 (C)
/Motor C/1A: A6.4 (1A), J12.3
/Motor C/1B: A6.3 (1B), J12.4
/Motor C/2A: A6.5 (2A), J12.2
/Motor C/2B: A6.6 (2B), J12.1
/Motor C/MS1: A6.10 (MS1), JP18.2 (C)
/Motor C/MS2: A6.11 (MS2), JP17.2 (C)
/Motor C/MS3: A6.12 (NC/TX), JP16.2 (C)
/Motor X1/1A: A7.4 (1A), J9.3
/Motor X1/1B: A7.3 (1B), J9.4
/Motor X1/2A: A7.5 (2A), J9.2
/Motor X1/2B: A7.6 (2B), J9.1
/Motor X1/MS1: A7.10 (MS1), JP21.2 (C)
/Motor X1/MS2: A7.11 (MS2), JP20.2 (C)
/Motor X1/MS3: A7.12 (NC/TX), JP19.2 (C)
/Motor X/1A: A1.4 (1A), J5.3
/Motor X/1B: A1.3 (1B), J5.4
/Motor X/2A: A1.5 (2A), J5.2
/Motor X/2B: A1.6 (2B), J5.1
/Motor X/MS1: A1.10 (MS1), JP3.2 (C)
/Motor X/MS2: A1.11 (MS2), JP2.2 (C)
/Motor X/MS3: A1.12 (NC/TX), JP1.2 (C)
/Motor Y/1A: A2.4 (1A), J2.3
/Motor Y/1B: A2.3 (1B), J2.4
/Motor Y/2A: A2.5 (2A), J2.2
/Motor Y/2B: A2.6 (2B), J2.1
/Motor Y/MS1: A2.10 (MS1), JP6.2 (C)
/Motor Y/MS2: A2.11 (MS2), JP5.2 (C)
/Motor Y/MS3: A2.12 (NC/TX), JP4.2 (C)
/Motor Z/1A: A4.4 (1A), J6.3
/Motor Z/1B: A4.3 (1B), J6.4
/Motor Z/2A: A4.5 (2A), J6.2
/Motor Z/2B: A4.6 (2B), J6.1
/Motor Z/MS1: A4.10 (MS1), JP12.2 (C)
/Motor Z/MS2: A4.11 (MS2), JP11.2 (C)
/Motor Z/MS3: A4.12 (NC/TX), JP10.2 (C)
/UART_A: A3.13 (PDN/RX), A3.14 (NC/CLK), A5.13 (PDN/RX), A5.14 (NC/CLK), A6.13 (PDN/RX), A6.14 (NC/CLK), J1.22 (GPIO25)
/UART_X: A1.13 (PDN/RX), A1.14 (NC/CLK), A2.13 (PDN/RX), A2.14 (NC/CLK), A4.13 (PDN/RX), A4.14 (NC/CLK), A7.13 (PDN/RX), A7.14 (NC/CLK), J1.29 (GCLK1/GPIO5)
GND: A1.1 (GND), A1.7 (GND), A2.1 (GND), A2.7 (GND), A3.1 (GND), A3.7 (GND), A4.1 (GND), A4.7 (GND), A5.1 (GND), A5.7 (GND), A6.1 (GND), A6.7 (GND), A7.1 (GND), A7.7 (GND), C1.2, C2.2, C3.2, C4.2, C5.2, C6.2, C7.1, C8.1, C9.1, C10.2, J1.20 (GND), J1.25 (GND), J1.30 (GND), J1.34 (GND), J1.39 (GND), J4.2, J8.2, J11.2, J13.2, J14.2, J15.2, J16.2, JP1.1 (A), JP2.1 (A), JP3.1 (A), JP4.1 (A), JP5.1 (A), JP6.1 (A), JP7.1 (A), JP8.1 (A), JP9.1 (A), JP10.1 (A), JP11.1 (A), JP12.1 (A), JP13.1 (A), JP14.1 (A), JP15.1 (A), JP16.1 (A), JP17.1 (A), JP18.1 (A), JP19.1 (A), JP20.1 (A), JP21.1 (A), U1.9 (VSS), U2.2 (GND), U2.8 (Rs)
MEN: A1.9 (~ENABLE), A2.9 (~ENABLE), A3.9 (~ENABLE), A4.9 (~ENABLE), A5.9 (~ENABLE), A6.9 (~ENABLE), A7.9 (~ENABLE), J1.15 (GPIO22)
unnamed: C7.2, U1.7 (OSC2), Y1.2
unnamed: C8.2, U1.8 (OSC1), Y1.1
unnamed: R1.1, U1.17 (~RESET)
Vin: A1.8 (VMOT), A2.8 (VMOT), A3.8 (VMOT), A4.8 (VMOT), A5.8 (VMOT), A6.8 (VMOT), A7.8 (VMOT), C1.1, C2.1, C3.1, C4.1, C5.1, C6.1, C10.1, J4.1

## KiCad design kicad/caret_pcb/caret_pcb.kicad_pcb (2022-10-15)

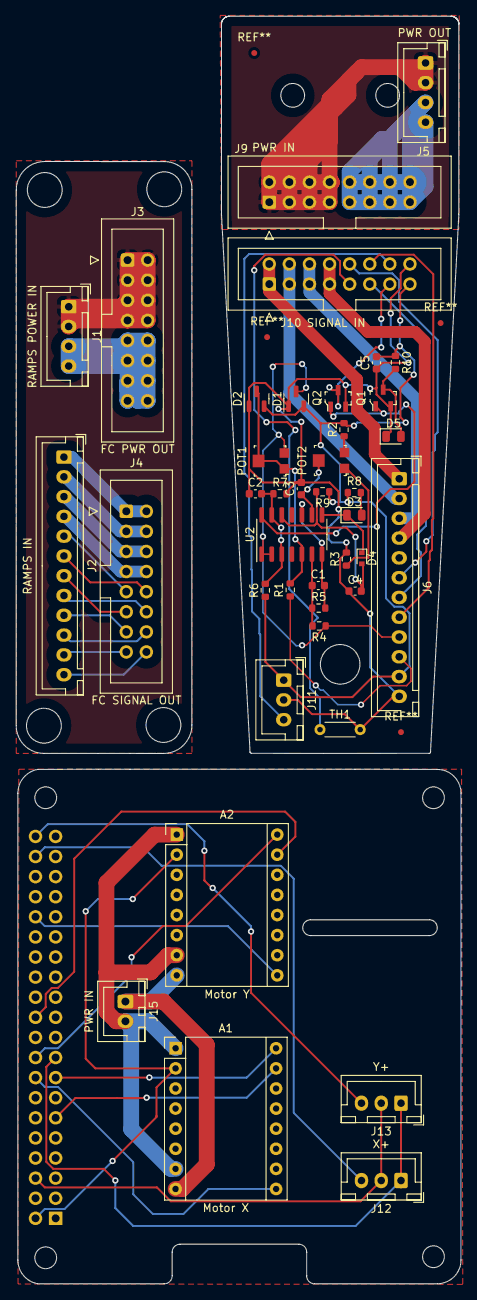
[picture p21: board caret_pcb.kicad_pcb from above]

Board: 2 copper layers, 56.2 x 160.2 mm, 41 parts (1 on the bottom side), 55 nets.

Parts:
A1: Motor X; Pololu_Breakout-16_15.2x20.3mm
A2: Motor Y; Pololu_Breakout-16_15.2x20.3mm
C1, C2, C3: 0.1uF; C_0603_1608Metric
C4, C5: 1 uF 10 V 10%; C_0603_1608Metric
D1, D2: BAV99; SOT-23
D3: RED; D_0805_2012Metric
D4: RB751S40T1G; D_SOD-523
D5: BLUE; D_0805_2012Metric
J1: RAMPS POWER IN; JST_XH_B4B-XH-A_1x04_P2.50mm_Vertical
J2: RAMPS IN; JST_XH_B12B-XH-A_1x12_P2.50mm_Vertical
J3: FC PWR OUT; IDC-Header_2x08_P2.54mm_Vertical
J4: FC SIGNAL OUT; IDC-Header_2x08_P2.54mm_Vertical
J5: PWR OUT; JST_XH_B4B-XH-A_1x04_P2.50mm_Vertical
J6: TOOLHEAD; JST_XH_B12B-XH-A_1x12_P2.50mm_Vertical
J9: PWR IN; IDC-Header_2x08_P2.54mm_Vertical
J10: SIGNAL IN; IDC-Header_2x08_P2.54mm_Vertical
J11: Endstop Y; JST_XH_B3B-XH-A_1x03_P2.50mm_Vertical
J12: X+; JST_XH_B3B-XH-A_1x03_P2.50mm_Vertical
J13: Y+; JST_XH_B3B-XH-A_1x03_P2.50mm_Vertical
J14: Raspberry_Pi_2_3; PinSocket_2x20_P2.54mm_Vertical
J15: PWR IN; JST_XH_B2B-XH-A_1x02_P2.50mm_Vertical
POT1: TC33X-2-105; Trimpot_3.8mmx3.6mm_TC33X-2-103E
POT2: TC33X-2-104; Trimpot_3.8mmx3.6mm_TC33X-2-103E
Q1, Q2: BSS138BK; SOT-23-3
R1, R6, R7: 10k; R_0603_1608Metric
R2: 330k; R_0603_1608Metric
R3: 390k; R_0603_1608Metric
R4: 20k; R_0603_1608Metric
R5: 82k; R_0603_1608Metric
R8: 510; R_0603_1608Metric
R9: 1M; R_0603_1608Metric
R10: 1k; R_0603_1608Metric
TH1: Thermistor_NTC; R_Axial_DIN0204_L3.6mm_D1.6mm_P5.08mm_Horizontal
U2: LM324; SOIC-14_3.9x8.7mm_P1.27mm

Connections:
/Caret Adapter/1A: J6.2, J10.3, J10.4
/Caret Adapter/1B: J6.1, J10.1, J10.2
/Caret Adapter/2A: J6.3, J10.5, J10.6
/Caret Adapter/2B: J6.4, J10.7, J10.8
/Caret Adapter/5V+: C5.2, D1.2 (A), D2.2 (A), J6.11, J10.15, J11.1, R2.2, R6.1, R8.1, R9.1, R10.1
/Caret Adapter/End.Y: J10.14, J11.3
/Caret Adapter/GND: C2.1, C3.2, C4.1, C5.1, D1.1 (K), D2.1 (K), D5.1 (K), J6.12, J10.16, J11.2, Q1.2 (S), Q2.2 (S), R3.2, R7.2, TH1.2
/Caret Adapter/HE0+: J5.1, J5.2, J9.1, J9.2, J9.3, J9.4, J9.5, J9.6, J9.7, J9.8
/Caret Adapter/PWM 5V: J6.8, J10.12
/Caret Adapter/PZ+: D1.3 (K), J6.9, POT1.3 (CW), R4.1, U2.1, U2.2 (-)
/Caret Adapter/PZ-: J6.10, R1.1
/Caret Adapter/T.enc: J10.9, TH1.1
/Caret Adapter/T.ext: J6.6, J10.10
/Caret Adapter/T.hbr: J6.7, J10.11
/Caret Adapter/Z+: J10.13, Q2.3 (D)
/RAMPS Adapter/+5V: J2.11, J4.15
/RAMPS Adapter/A3/T.hbr: J2.7, J4.11
/RAMPS Adapter/A4/T.ext: J2.6, J4.10
/RAMPS Adapter/A13/T.enc: J2.5, J4.9
/RAMPS Adapter/D6/PWM 5V: J2.8, J4.12
/RAMPS Adapter/D39/End.Y: J2.10, J4.14
/RAMPS Adapter/D45/End.Z: J2.9, J4.13
/RAMPS Adapter/E0 1A: J2.2, J4.3, J4.4
/RAMPS Adapter/E0 1B: J2.1, J4.1, J4.2
/RAMPS Adapter/E0 2A: J2.3, J4.5, J4.6
/RAMPS Adapter/E0 2B: J2.4, J4.7, J4.8
/RAMPS Adapter/GND_RAMPS: J2.12, J4.16
/RAMPS Adapter/HE0+: J1.1, J1.2, J3.1, J3.2, J3.3, J3.4, J3.5, J3.6, J3.7, J3.8
/RPi Motor/GNDmot: A1.1 (GND), A1.7 (GND), A2.1 (GND), A2.7 (GND), J15.2
/RPi Motor/MotX DIR: A1.16 (DIR), J14.15 (GPIO22)
/RPi Motor/MotX En: A1.9 (~ENABLE), J14.16 (GPIO23)
/RPi Motor/MotX Step: A1.15 (STEP), J14.11 (GPIO17)
/RPi Motor/MotY DIR: A2.16 (DIR), J14.18 (GPIO24)
/RPi Motor/MotY En: A2.9 (~ENABLE), J14.32 (PWM0/GPIO12)
/RPi Motor/MotY Step: A2.15 (STEP), J14.22 (GPIO25)
/RPi Motor/Vmot: A1.8 (VMOT), A2.8 (VMOT), J15.1
/RPi Motor/X+: J12.3, J14.38 (GPIO20/MOSI1)
/RPi Motor/Y+: J13.3, J14.40 (GPIO21/SCLK1)
GND1: J5.3, J5.4, J9.9, J9.10, J9.11, J9.12, J9.13, J9.14, J9.15, J9.16
GNDREF: J1.3, J1.4, J3.9, J3.10, J3.11, J3.12, J3.13, J3.14, J3.15, J3.16
unnamed: A1.2 (VDD), A2.2 (VDD), J14.4 (5V)
unnamed: C1.1, R4.2, R5.1, U2.6 (-)
unnamed: C1.2, R5.2, U2.7, U2.10 (+)
unnamed: C2.2, R6.2, R7.1, U2.3 (+), U2.13 (-)
unnamed: C3.1, POT2.2 (Wiper), U2.9 (-)
unnamed: C4.2, D4.2 (A), R9.2, U2.12 (+)
unnamed: D2.3 (K), POT1.1 (CCW), POT1.2 (Wiper), R1.2, U2.5 (+)
unnamed: D3.1 (K), D4.1 (K), U2.8
unnamed: D3.2 (A), R8.2
unnamed: D5.2 (A), Q1.3 (D), R10.2
unnamed: J12.1, J13.1, J14.17 (3V3)
unnamed: J12.2, J13.2, J14.6 (GND)
unnamed: POT2.1 (CCW), R3.1
unnamed: POT2.3 (CW), R2.1
unnamed: Q1.1 (G), Q2.1 (G), U2.14

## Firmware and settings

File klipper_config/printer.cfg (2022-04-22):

[include client.cfg]
[include heaters.cfg]
[include client_macros.cfg]
[include printer_bed_mesh_tilt.cfg]


[idle_timeout]
timeout: 3600

[force_move]
enable_force_move: True

[filament_motion_sensor sfs]
detection_length: 10.0
#   The minimum length of filament pulled through the sensor to trigger
#   a state change on the switch_pin
#   Default is 7 mm.
extruder: extruder
#   The name of the extruder section this sensor is associated with.
#   This parameter must be provided.
switch_pin: ^ar3
pause_on_runout: True
#runout_gcode:
#insert_gcode:
#event_delay:
#pause_delay:
#   See the "filament_switch_sensor" section for a description of the
#   above parameters.

[probe]
#pin: ^ar57
pin: ^!ar18
#sensor_pin: ar19
x_offset: 0
y_offset: 0
z_offset: 0

speed: 6.0
samples: 1
sample_retract_dist: 4.0
samples_tolerance: 0.025
samples_tolerance_retries: 3

activate_gcode: G4 P500




[homing_override]
set_position_z:0
gcode:
  G1 Z10 F500
  G28 X Y
  G1 X270 Y270 F6000
  G28 Z
#  Z_TILT_ADJUST
##  BED_MESH_CALIBRATE
  g1 z5
#  G1 X250 Y250 F3000

[mcu host]
serial: /tmp/klipper_host_mcu



[stepper_y]
# endstop_pin: ^host:gpio16
endstop_pin: ^host:gpio21
position_endstop: 0
position_max: 550

# OLD
# enable_pin: host:gpio19
# step_pin: host:gpio2
# dir_pin:  host:gpio17

# Макетка-шилд
# старое
enable_pin: host:gpio12
step_pin: host:gpio25
dir_pin:  host:gpio24
# enable_pin: host:gpio23
# step_pin: host:gpio17
# dir_pin: !host:gpio22

step_distance: .01

homing_speed: 80
homing_retract_dist: 5
second_homing_speed: 2.5


[stepper_x]
# endstop_pin: ^!host:gpio26
endstop_pin: ^!host:gpio20
position_endstop: 540
position_max: 540

# OLD
# enable_pin: host:gpio19
# step_pin: host:gpio27
# dir_pin: !host:gpio18

# Макетка-шилд
# старое
enable_pin: host:gpio23
step_pin: host:gpio17
dir_pin: !host:gpio22
# enable_pin: host:gpio12
# step_pin: host:gpio25
# dir_pin:  host:gpio24

step_distance: .01
homing_speed: 80
homing_retract_dist: 5
second_homing_speed: 2.5



# See schematic of RAMPS:
# https://reprap.org/mediawiki/images/f/f6/RAMPS1.4schematic.png
# 
[tmc2130 stepper_z]
cs_pin: ar66
run_current: 1.0
hold_current: 0.4

[stepper_z]
# Посадочное место X
# step_pin: ar54
# dir_pin: ar55
# enable_pin: !ar38

# RAMPS E1 Driver socket
step_pin: ar36
dir_pin: ar34
enable_pin: !ar30

# step_distance: .0025
# microsteps: 2
step_distance: .000625
microsteps: 8
endstop_pin: probe:z_virtual_endstop
#position_endstop: 0
position_max: 550
homing_speed: 6
second_homing_speed: 6
position_min: -50


[tmc2130 stepper_z1]
cs_pin: ar40
run_current: 1.0
hold_current: 0.4

# RAMPS Y(???) Driver
[stepper_z1]
step_pin: ar60
dir_pin: ar61
enable_pin: !ar56
step_distance: .000625
microsteps: 8
#endstop_pin: ^!ar14


[tmc2130 stepper_z2]
cs_pin: ar42
run_current: 1.0
hold_current: 0.4

# RAMPS Z Driver socket
[stepper_z2]
step_pin: ar46
dir_pin: !ar48
enable_pin: !ar62
step_distance: .000625
microsteps: 8
#endstop_pin: ^!ar18



[mcu]
#serial: /dev/ttyACM0
serial: /dev/serial/by-id/usb-1a86_USB_Serial-if00-port0
# serial: /dev/serial/by-id/usb-1a86_USB_Serial-if00-port0
pin_map: arduino

[printer]
kinematics: corexy
max_velocity: 250
max_accel: 20000
max_accel_to_decel: 20000
max_z_velocity: 7
max_z_accel: 100

# Common EXP1 / EXP2 (display) pins
[board_pins]
aliases:
    # Common EXP1 header found on many "all-in-one" ramps clones
    EXP1_1=ar37, EXP1_3=ar17, EXP1_5=ar23, EXP1_7=ar27, EXP1_9=<GND>,
    EXP1_2=ar35, EXP1_4=ar16, EXP1_6=ar25, EXP1_8=ar29, EXP1_10=<5V>,
    # EXP2 header
    EXP2_1=ar50, EXP2_3=ar31, EXP2_5=ar33, EXP2_7=ar49, EXP2_9=<GND>,
    EXP2_2=ar52, EXP2_4=ar53, EXP2_6=ar51, EXP2_8=ar41, EXP2_10=<RST>
    # Pins EXP2_1, EXP2_6, EXP2_2 are also MISO, MOSI, SCK of bus "spi"
    # Note, some boards wire: EXP2_8=<RST>, EXP2_10=ar41

[display]
lcd_type: st7920
cs_pin: EXP1_4
sclk_pin: EXP1_5
sid_pin: EXP1_3
encoder_pins: ^EXP2_3, ^EXP2_5
click_pin: ^!EXP1_2
#kill_pin: ^!EXP2_8

[output_pin beeper]
pin: EXP1_1

[gcode_macro M300]
default_parameter_S: 1
#   Use a default 1kHz tone if S is omitted.
default_parameter_P: 100
#   Use a 10ms duration is P is omitted.
gcode:
    SET_PIN PIN=beeper VALUE={S}
    G4 P{P}
    SET_PIN PIN=beeper VALUE=0

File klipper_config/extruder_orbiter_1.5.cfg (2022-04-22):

[tmc2130 extruder]
# cs_pin: ar40
cs_pin: ar65
# spi_software_sclk_pin: ar44
# spi_software_mosi_pin: ar42
# spi_software_miso_pin: ar64
run_current: 0.5
hold_current: 0.2


[extruder]
step_pin: ar26
dir_pin: !ar28
enable_pin: !ar24

microsteps: 16
# базовая экструзия
#step_distance: .001420610687023
# на 5% больше экструзия
step_distance: .001491641221374
# на 2% меньше экструзия
# step_distance: .00145

# на 5% больше экструзии
#step_distance: .0013775

# step_distance: .001526717557252
nozzle_diameter: 0.600
filament_diameter: 1.750

max_extrude_only_distance: 100.0

heater_pin: ar10
sensor_type: ATC Semitec 104GT-2
# sensor_type: NTC 100K beta 3950
# sensor_type: EPCOS 100K B57560G104F
sensor_pin: analog13
control: pid
# для 250ºC / 40W
#pid_Kp=23.012 
#pid_Ki=0.892 
#pid_Kd=148.430
# для 250ºC / 144W
#pid_Kp=12.570 
#pid_Ki=0.415 
#pid_Kd=95.215

# Для 250ºC / 50W / Volcano
# pid_Kp=36.847 
# pid_Ki=1.342 
# pid_Kd=252.865

# Для 250ºC / 75W / Mosquito Magnum с кабелем который был частично перебит
# pid_Kp=26.278 
# pid_Ki=1.788 
# pid_Kd=96.571

# Для 250ºC / 75W / Mosquito Magnum с нормальным кабелем
# pid_Kp=26.278 
# pid_Ki=1.752 
# pid_Kd=98.542

# Для 250ºC / 75W * 2 / Mosquito Magnum+ 0.8mm
pid_Kp=12.916 
pid_Ki=0.439 
pid_Kd=94.934

min_temp: 0
max_temp: 350
min_extrude_temp: 0

# Для HTP ABS+ 280ºC
# pressure_advance = 0.0595

# Для FDPlast ABS 260ºC на Volcano
# pressure_advance = 0.0417

# Для FDPlast ABS 250ºC на Mosquito Magnum+ 0.8mm 
pressure_advance = 0.033
#pressure_advance = 0.029

# Volcano
# [input_shaper]
# # 120 * 2 / 8.22
# shaper_freq_x: 37.69
# # 120 * 4 / 18.7
# shaper_freq_y: 25.06
# shaper_type: mzv


# Mosquito Magnum Plus
[input_shaper]
# 150 * 3 / 11.76
shaper_freq_x: 38.26
# 150 * 3 / 10.1
shaper_freq_y: 44.55
shaper_type: mzv

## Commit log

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2020-08-02 changed gantries and added dxfs
    [plates.scad, x-axis.scad, z-axis.scad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]
2020-11-01 rev 1: почти всё есть кроме корпуса + недоделанный fan duct
    [3dtouch_Probe.stl, Adapt_carriage.stl, Attache_cable.stl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]
2020-11-02 fix x axis mirror and duct render
    [fan_duct.scad, x-axis.scad, y-axis.scad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]
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2020-11-04 fixes to fun duct
    [fan_duct.scad, x-axis.scad]
2020-11-04 funduct stl + blower vitamin
    [fan_duct.scad]
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2020-11-15 added titan extruder model
    [electronics_box.scad, extruder_mount.scad, x-axis.scad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]
2021-01-26 double rail printhead work
    [carets.scad, extruder_mount.scad, x-axis.scad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]
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2021-03-09 версия с 2 рельсами
    [E3D_V6_40mm_Fan_v2.stl, ECBC_belt_clamp.stl, carets.scad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]
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2021-03-16 голова шпинделя, в целом готвая каретка X
    [carets.scad, extruder_mount.scad, fan_duct.scad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]
2021-03-18 extruder toolhead and caret belt lock part
    [carets.scad, extruder_heatbreak_cooler.scad, extruder_mount.scad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]
2021-03-20 fix mount holes on X caret
    [x-axis.scad]
2021-03-21 added v6 collet lock to extruder toolhead
    [extruder_mount.scad]
2021-03-28 added v6 ptfe collet
    [extruder_mount.scad]
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2021-04-26 new heat bed wip; refactor toolhead utils; new spindle toohead plates and piezo
    [extruder_mount.scad, heat_bed_heater.scad, heatbed.scad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]
2021-04-26 fix assymbly preview
    [spindle_mount.scad]
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2021-05-07 new z axis and heatbed
    [heatbed.scad, z-axis.scad]
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2021-05-08 fix spool rod nuts
    [spool_holder.scad]
2021-05-08 z gantry holder should have mounts for PC part
    [heatbed.scad]
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2021-05-08 z_gantry mini rail mount hole for tapping
    [z-axis.scad]
2021-05-09 z_gantry fix lead screw mounts
    [z-axis.scad]
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2021-05-16 thrust bearing support for z axis
    [z-axis.scad]
2021-05-16 correct stl for spindle collet
    [spindle_mount.scad]
2021-05-30 z axis top pillow block
    [z-axis.scad]
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2021-05-30 fix wheels distance; y caret now has 4 wheels and centered belts
    [carets.scad]
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2021-06-20 toolhead_extruder: add orbiter, upgrade e3d heatberak cooler mount, refactoring
    [toolhead_extruder_generic.scad, toolhead_extruder_heatbreak_e3d_cooler.scad, toolhead_extruder_orbiter.scad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]
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2021-11-08 hotend_mosquito: fix rotation and add dimension functions
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2021-11-08 fan_duct: add splitter for double hose nozzle cooling
    [fan_duct.scad]
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2021-11-08 toolhead_extruder: added mosquito cooler case wip
    [toolhead_extruder_heatbreak_mosquito_cooler.scad]
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2021-11-27 removed stale stl files
    [electronics_box.stl, preicision_piezo_throat.stl]
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2021-11-27 toolheads: mosquito small fixes
    [toolhead_extruder_heatbreak_mosquito_cooler.scad, toolhead_extruder_orbiter_mosquito.scad]
2021-11-27 toolheads: fixed spindle toolhead errors
    [toolhead_spindle.scad, toolhead_utils.scad]
2021-11-27 x-axis: fixed errors after gantry refactoring
    [x-axis.scad]
2021-11-27 x-axis: encapsulate working space and safe margins calculation
    [x-axis.scad]
2021-11-27 y-axis: encapsulate working space and safe margins calculation
    [carets.scad, y-axis.scad]
2021-11-28 z-axis: encapsulate working space and safe margins calculation
    [y-axis.scad, z-axis.scad]
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2021-11-28 3d_printer: add main assembly
    [carets.scad, heatbed.scad, main_cnc_router.scad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]
2021-11-29 3d_printer: add x/y motor plates and corner belt pulley plates
    [heatbed.scad, main_km_3d_printer.scad, motors.scad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]
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2021-11-29 heatbed: fix vitamin name
    [heatbed.scad]
2021-11-29 frame: add belt corner pulleys assembly with 3d printed spacers
    [main_km_3d_printer.scad, pulley_and_motor_plates.scad, pulley_spacer.scad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]
2021-11-29 3d_printer: corexy belt and pulleys
    [main_km_3d_printer.scad, pulley_and_motor_plates.scad, y-axis.scad]
2021-11-29 z-axis: correct height
    [main_km_3d_printer.scad, x-axis.scad, y-axis.scad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]
2021-11-29 y-axis: fix caret positioning
    [y-axis.scad]
2021-11-29 heatbed: support rectangular shape
    [heatbed.scad, main_km_3d_printer.scad, pulley_and_motor_plates.scad]
2021-11-29 enclosure: front and rear case parts
    [enclosure_full.scad, main_km_3d_printer.scad]
2021-11-30 enclosure: all parts except bottom
    [case_plates.scad, enclosure_full.scad, main_km_3d_printer.scad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]
2021-12-01 enclosure: almost done all parts + refactoring
    [enclosure_assembly.scad, enclosure_back.scad, enclosure_bottom.scad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]
2021-12-01 x-axis: improve performance with pure 2d shapes
    [x-axis.scad]
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2021-12-05 z-axis: add anti-wobble rings
    [z-axis.scad]
2021-12-05 z-axis: remove global constant
    [z-axis.scad]
2021-12-22 enclosure: z-axis mounts + reworked side windows
    [enclosure_assembly.scad, enclosure_sides.scad, enclosure_vslot_mounts.scad]
2021-12-22 enclosure: x/y motor windows
    [enclosure_sides.scad, main_km_3d_printer.scad]
2022-01-15 heat_bed_heater: support different material types
    [heat_bed_heater.scad]
2022-03-06 everything: lots of changes
    [belt_pulley.scad, belt_pulleys.scad, electronics_box.scad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]
2022-03-07 enclosure: top part corner extrusions
    [enclosure_assembly.scad, enclosure_back.scad, enclosure_bottom.scad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]
2022-03-08 enclosure: polycarbonate parts done
    [enclosure_assembly.scad, enclosure_common.scad, enclosure_doors.scad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]
2022-03-13 multiple: six stl exports
    [electronics_box.scad, main_km_3d_printer.scad, pulley_and_motor_plates.scad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]
2022-03-13 enclosure: fix gaslift mount
    [enclosure_sides.scad]
2022-03-21 motor plates: change screw to be screwed from top
    [pulley_and_motor_plates.scad]
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2022-03-21 leadscrew_anti_z_wobble: in nut mount part fixed leadscrew hole, fixed mount cylinders height
2022-03-21 enclosure_sides: motors side — swapped elevation of x/y motors and, motor plate windows now count coloring thickness
    [enclosure_sides.scad]
2022-03-21 enclosure_front: hinge now has 3 mounts
    [enclosure_doors.scad, enclosure_front.scad, parametric_hinge_door_front.scad]
2022-03-21 enclosure_back: hinge now has 3 mounts, fixed misplaced hinge mounts on enclosure
    [enclosure_back.scad, enclosure_doors_top.scad, parametric_hinge_door_top.scad]
2022-03-21 enclosure_front: fix magnet positioning at front doors and add magnets to bom
    [enclosure_assembly.scad, enclosure_doors.scad, toolhead_utils.scad]
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2022-03-22 z-axis: fix z ganry table mount block
    [z-axis.scad]
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2022-03-28 toolhead_extruder_orbiter: fix some issues
    [toolhead_extruder_generic.scad, toolhead_extruder_heatbreak_mosquito_cooler.scad, toolhead_extruder_orbiter_mosquito.scad]
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2022-03-28 electronics_box.scad: fixed case vesa mount, added sensor cover mount
    [electronics_box.scad, filament_sensor_cover_bmg.stl]
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2022-04-04 electronics_box.scad: fix screws
    [electronics_box.scad]
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2022-07-06 toolhead_extruder_heatbreak_mosquito_cooler.scad: moved piezo disc location to bottom for better sensitivity
    [toolhead_extruder_heatbreak_mosquito_cooler.scad, toolhead_utils.scad]
2022-07-06 toolhead_extruder_heatbreak_mosquito_cooler.scad: fix cooling part
    [toolhead_extruder_heatbreak_mosquito_cooler.scad]
2022-07-06 toolhead_extruder_heatbreak_mosquito_cooler.scad: fixed wire mounts and moved piezo disk to new location
    [toolhead_extruder_heatbreak_mosquito_cooler.scad]
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2022-07-07 caret_cable_chain: size fixes
    [caret_cable_chain.scad, enclosure_sides.scad, x-axis.scad]
2022-07-07 caret_pcb: fix power line
    [caret_pcb.kicad_pcb, caret_pcb.kicad_sch, caret_piezo_sensor.kicad_sch]
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2022-10-15 caret_pcb: fix piezo sensor power line, fix rpi shield schematic
    [caret_pcb.kicad_pcb, caret_pcb.kicad_sch, caret_piezo_sensor.kicad_sch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]
2022-11-11 cnc_router: dxf fixes
    [main_cnc_router.scad]
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2022-11-11 toolhead_extruder_heatbreak_mosquito: fix stl namings
    [toolhead_extruder_heatbreak_mosquito_cooler.scad]
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2022-11-29 toolhead_spindle_generic_plastic: fix latch height
    [toolhead_spindle_generic_plastic.scad]
2022-12-23 main_cnc_router: fix z gantry
    [main_cnc_router.scad]
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2023-01-25 heatbeds: refactoring, moved to common tool tables package common for work surfaces
    [ceramic_granite_heatbed_table.scad, concrete_heatbed_table.scad, heat_bed_heater.scad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]
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2023-06-04 rpi_motor_pcb: 6-axis fix diag pin, add en pin
    [mosfet_gpio.kicad_sch, rpi_motor_pcb.kicad_pcb, rpi_motor_pcb.kicad_sch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]
2023-06-04 rpi_motor_pcb: 7-axis canbus version (removed useless fan and limit switch)
    [rpi_motor_pcb.kicad_pcb, rpi_motor_pcb.kicad_sch, tmc2208_driver_socket.kicad_sch]
2023-06-04 rpi_motor_pcb: fix ms hints
    [rpi_motor_pcb.kicad_pcb]
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2023-07-16 heater_pcb: fix errors
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2023-12-31 lib: complete migration to vslot_wheels and cable shain library
    [carets.scad, electronics_box.scad, enclosure_assembly.scad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]
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2023-12-31 fix import errors
    [enclosure_vslot_mounts.scad, z-axis.scad]
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2024-02-27 fix enclosure refactoring warnings
    [enclosure_assembly.scad, enclosure_back.scad, enclosure_front.scad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]
2024-02-28 caret_pcb: fix import
    [tool_extruder.kicad_sch, tool_motor.kicad_sch]
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
